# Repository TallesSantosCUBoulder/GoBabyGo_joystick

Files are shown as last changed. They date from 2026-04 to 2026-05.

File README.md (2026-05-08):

# GoBabyGo Joystick-Controlled Car
**ENGR140: First Year Engineering Projects - Colorado Mesa University**  
**Sponsor:** Talles Santos  
**Project Team:** Team Snow Munchers  
**Team Members:** Michael Riley (Civil Engineering)  
&emsp;&emsp;&emsp;&emsp;&emsp;&emsp;&emsp;&emsp; Francisco Cuen (Mechanical Engineering)  
&emsp;&emsp;&emsp;&emsp;&emsp;&emsp;&emsp;&emsp; Jaclyn Pellegrini (Mechanical Engineering)  
&emsp;&emsp;&emsp;&emsp;&emsp;&emsp;&emsp;&emsp;Caleb Kasayka (Mechanical Engineering)  
&emsp;  
&emsp;
&emsp;  
**Note: A large part of this README file references the [User Manual](/Reports/Users%20manual.pdf) and [Final Report](/Reports/Final%20Report%20First%20Draft%20-%20Snow%20Munchers.pdf) written by the members of the Snow Munchers Team. The printed circuit board (PCB) was designed, and the README was written and compiled, by Electrical and Computer Engineering Senior [Alyssa Jackson](https://github.com/aJax-EXE).**

## Introduction
“GoBabyGo” is a non-profit organization dedicated to providing children with limited mobility the opportunity to play independently by adapting motorized toy cars. Many children with mobility challenges struggle to press the pedal and steer simultaneously, making it difficult to operate the vehicle without constant assistance. Typical “GoBabyGo” modifications reroute the pedal wiring to a button mounted on the steering wheel, simplifying acceleration and improving usability.  

After multiple iterations, the final design operated successfully and remained within budget. It reliably controlled forward/backward motion and steering, and testing showed consistent performance with minimal drift. The system was safe, intuitive, and easy for children to use. Future work should focus on simplifying the steering circuit and adapting the design for broader use across different ride‑on car models to benefit more children.  

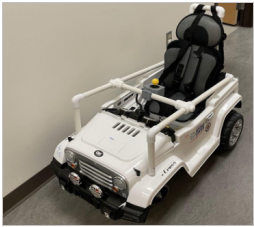
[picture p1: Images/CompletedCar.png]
Image of the Completed Car
  
*A standin image of the completed modified car*  

## Project Overview
While the standard modifications help many children, some still find it difficult to press a button and steer at the same time. This project aims to create a more intuitive control system by replacing both the pedal and steering wheel with a single joystick. The joystick must control forward and backward motion as well as left and right steering, operate safely under 12 V and 3 A, and be implemented for under $200.  

### Design Requirements
Along with the functions that the car needs to reach from the the project overview, the following and specific requirements were needed:  
* Directional Control
    * Provide forward, reverse, left, and right motion; each direction successfully actuates correct motor behavior 10/10 trials with a response rate of .5 seconds. 
* Consistent Steering & Speed Response
    * Vehicle follows the same path in 5 repeated trials within acceptable tolerance (e.g., ±6 inches lateral drift over 10-15ft).
* 12V Maximum Power
    * Must not exceed 12V thought out the electrical system.
* Dashboard Fit
    * Total joystick assembly dimensions must not exceed 2.75 in (height) × 3.125 in (width). Zero interference points and no natural obstructions.
* Heat Limit
    * Must not exceed 113° over 15 minute time intervals.

###  Electrical Solutions
For this car, a modification was made for the movement. Using a joystick instead of a steering wheel and foot-powered pedals, the car can move forwards and backwards without restrictions, but turning left and right is altered. Instead of turning left and right without restriction, moving or holding the joystick in either direction causes the car to turn for only a set amount of time before stopping and waiting for another input. __This is to help keep the motors from stalling as ... ? (Include a video/gif of the car moving in all four directions with the joystick)__  

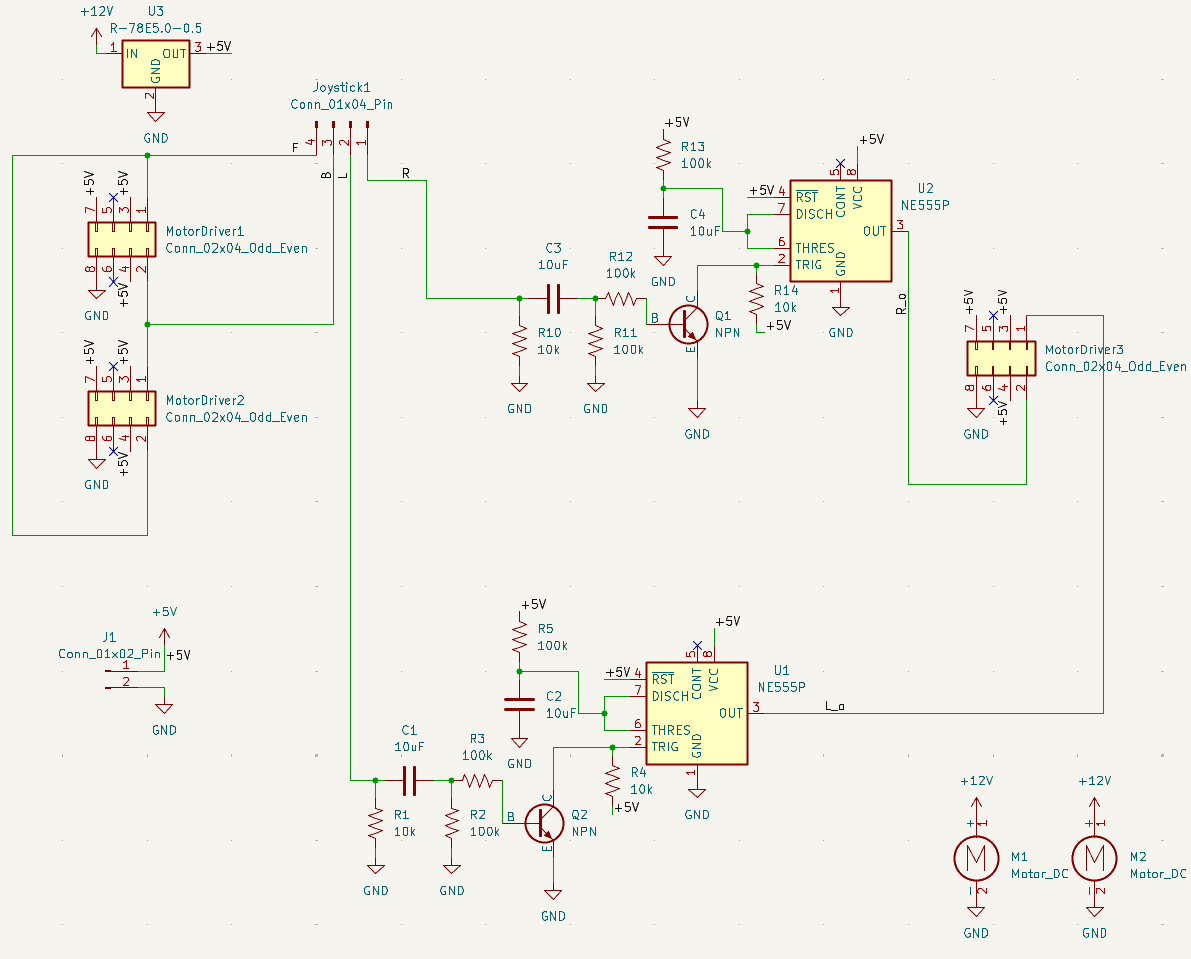
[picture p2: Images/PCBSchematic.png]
Full Car Circuit Diagram
  
*The Full Circuit Diagram of the car*  
&emsp;  

The full construction of the circuit requires the following components:
* [3 IBT-2 BTS7960 High Current H-Bridge Motor Drivers](/Datasheets/BTS7960%20Motor%20Driver.pdf)  
&emsp;  
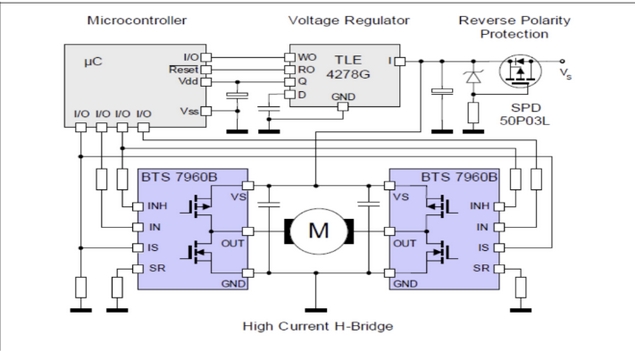
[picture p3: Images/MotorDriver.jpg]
H-Bridge Controller Diagram
      
    *The Function diagram of an H-Bridge Controller*  
    &emsp;  

    * Full representation of the function of an H-Bridge Controller can be found in the above image. When an input is received, it sends a signal to the H-bridge motor controller which recognizes the voltage as a directional input and then outputs that signal into the motor itself. This allows for safe, effective, bi-directional movement. The H-bridge has a total of 12 attachment points. two for power in, two for power to motor, two for input detection (seen as “IN”), two for inhibiting direction (“INH”, two for ISs), a ground for the logic board (GND), and a 5.5V input for the logic board (“VCC”). This design will take advantage of all the inputs / outputs except for the SIs.
* [2 LM555 Timer Chips](/Datasheets/lm555.pdf)  
&emsp;  
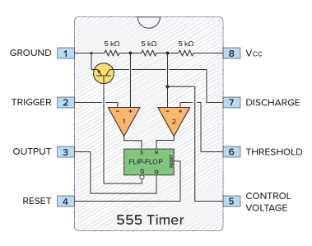
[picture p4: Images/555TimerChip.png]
555 Timer Chip Diagram
      
    *Diagram of a 555 timer and the respective pins*  
    &emsp;  

    * A 555 timer is an integrated circuit that takes an electrical input and outputs a pulse over a certain interval of time. This component is needed to turn the front steering motor to a certain point so that the motor doesn’t overturn the mechanical component, breaking the car, and burning out the motor. Power is inputted through the VCC pin which powers the circuit (as seen in the above image). When a signal comes through the Trigger pin, it goes through the circuit within the 555 and then a capacitor and resistor attached to the discharge and threshold pins which controls how long a pulse is sent out of the output pin. For this project, the 555 is operated in monostable mode, meaning it sends out a singular pulse and then returns to its original state. To get the pulse to last for a certain time, the equation T=1.1RC where T is time, R is the strength of the resistor, and C is the value of the capacitor. For the motor a 1 second pulse is needed so values of a100kΩ resistor and a 10µF capacitor are needed.
* [A Joystick](/Datasheets/SANWA%20JLF-TP-8YT%20Joystick%20Instruction%20Manual.pdf)  
&emsp;  
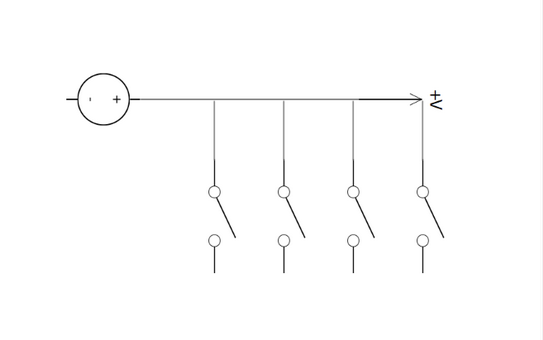
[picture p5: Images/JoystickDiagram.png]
Joystick Switch Diagram
      
    *Internal switching logic of the arcade joystick*  
    &emsp;  

    * The above image illustrates the internal switching logic of the joystick. The joystick has five wires with a gauge of 23 AWG (American Wire Gauge). These wires are connected to a circuit board via a connector. This system consists of four signal wires, each for a different switch that is also connected to the circuit board. The last wire serves as a 5V-12V source wire; the input (5V-12V) will flow through this wire and in return, will output through one of the four switches (possibly two) depending on which switch is compressed or activated. 
* [An RC Car](/Datasheets/BCP%20Sky908%20User%20Manual.pdf)
    * For this project an existing car was bought and provided to the group, but the car model used costs around $250 USD.

* [2 NPN Bipolar Junction Transistors](/Datasheets/2n2222a.pdf)  
&emsp;  
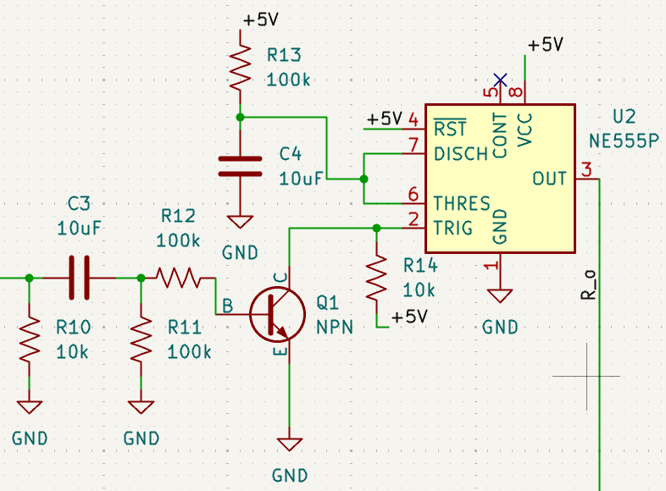
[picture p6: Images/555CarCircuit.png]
Diagram of timing circuit
      
    *The circuit diagram of the pulse shaping module used in the car*  
&emsp;  
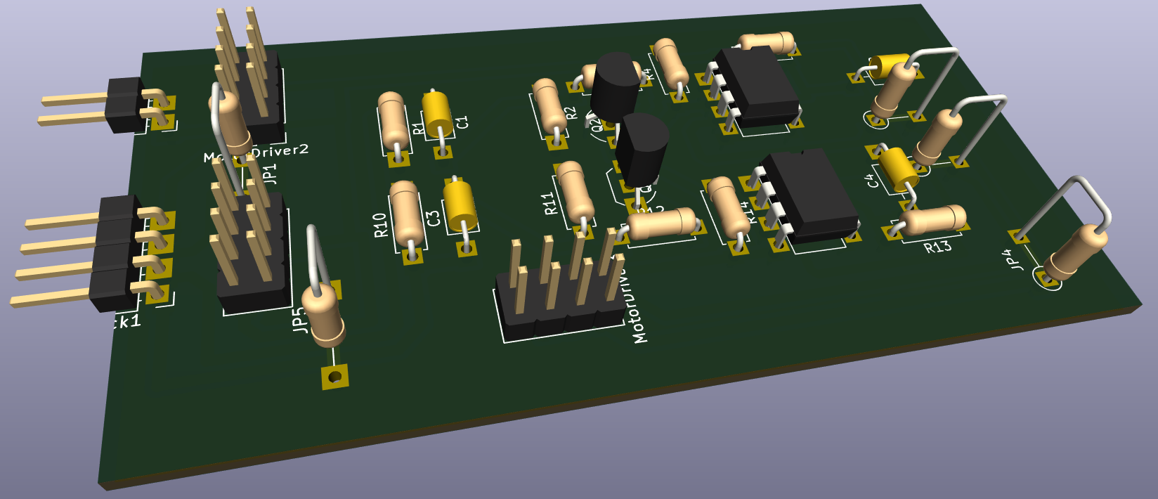
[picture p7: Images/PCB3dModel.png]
3D Model of the working PCB
      
    *The 3D Model that represents what the working model looks like*  
&emsp;  

    * The transistors are the necessary part of the timing circuit. For the 555 to properly work, it needs sharp, high input. This is not as simple as it would seem because our joystick is mainly used in a “toggle” sense, where the driver will hold it left to turn left. After some testing, we realized that this toggled system would lead to the output of the 555 system always being held high. To fix this, we implemented what is called a pulse shaping module. This consists mainly of a capacitor momentarily allowing a transistor to drain a power source to ground, creating a quick pulse of electricity that the 555 timers can properly understand. The above images shows the pulse shaping module implemented into the design of the circuit and the 3D model of the completed PCB with all of its components.  
* [Joystick Mount](/3dModels/Joystick%20Mount%203.STL)
&emsp;  
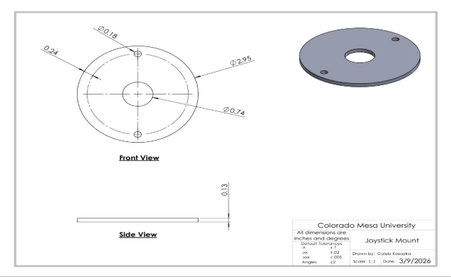
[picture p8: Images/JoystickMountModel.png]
Joystick Mount Solidworks Model
      
    *The SolidWorks drawing of the joystick mount*  
    &emsp;  

    * The joystick already has two existing mounting holes, 0.278 inches in diameter, implemented into the factory design. With this, a CAD drawing was produced and integrated with these existing holes (see Appendix E). The design functions similar to a washer where it will mount on the original steering wheel location. Two bolts will run through the top (the side where the joystick extrudes), and below there will be two nuts securing the simple assembly in place. The above image consists of a SolidWorks drawing of the mount.  
* A 12V to 5V Voltage Step Down
    * Must be able to handle 3A of current and 15W of power.
* 6 100k Ohm Resistors
* 4 10k Ohm Resistors
* 4 10uF Capacitors
* A 12V Battery
    * The model of car used includes a 12V 7AH battery. Most electric kid cars run on 6V, but this system is designed for 12V. To use this system with a 6V battery, a voltage step down that goes from 6V to 5V, or rather a simple voltage divider, needs to be used to run the system properly.
* 2 Rolls of 20 AWG Wire
    * One red and one black preferred.  
* Female to Female Jumper wires  

The circuit starts at the battery going into the two gearboxed motors of the car and the voltage step down. The 5V from the stepdown powers the rest of the system: all three of the motor drivers and the two 555 timer circuits. While the forward and backwards motor drivers are only activated with the direct signal from the joystick, the left and right one first goes through there respective timing circuit to give the proper timed signal.  

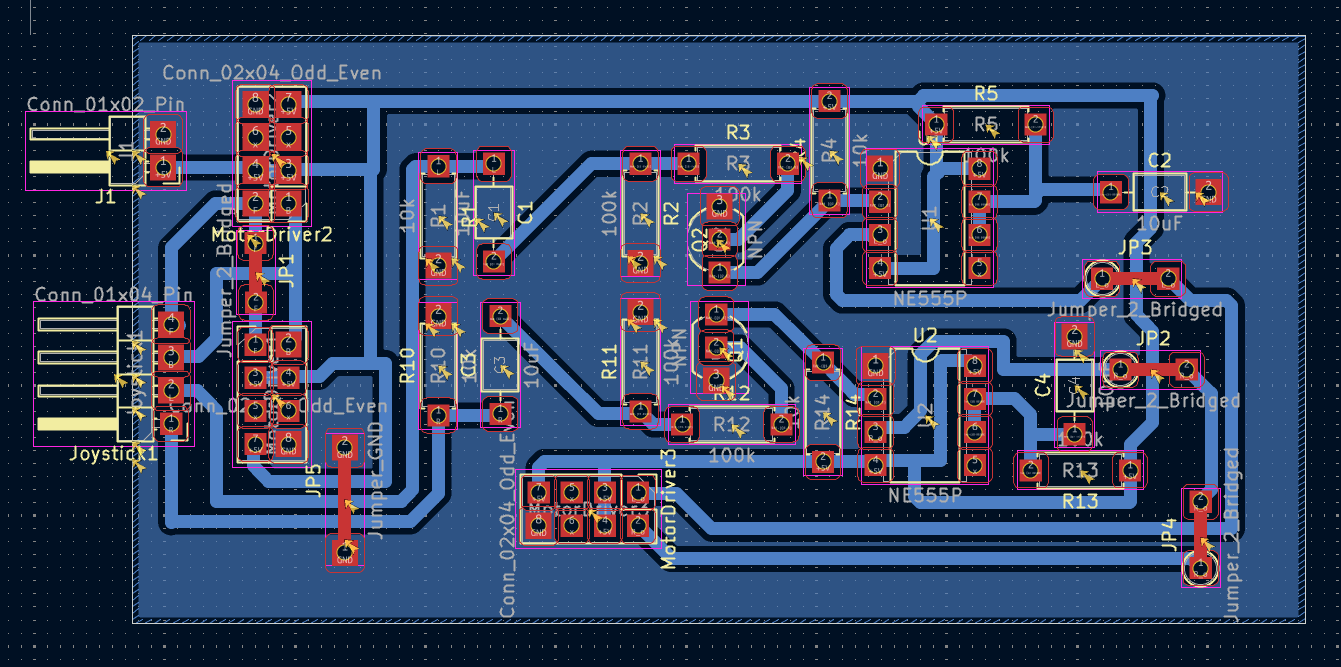
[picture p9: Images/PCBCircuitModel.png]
Full Car PCB Model
  
*The Full PCB model for the car*  
&emsp;  

The PCB holds the resistors, capacitors, and transistors that make up the timing circuit, as well as all of the connectors necessary for both powering the board, connecting the joystick to the motor drivers, and for the motor drivers themselves.

## Hardware Setup and How to Operate
For the complete instructions on how to modify the car to replicate the project, perform maintainence, and for a full list of tools needed and how to use, refer to the [User Manual](/Reports/User%20Manual%20Outline.pdf) written by the Snow Munchers.

### Recommendations for Operation
Before general use, it is recommended that:  
* The driver does not exceed 77lbs
* The car avoids liquid 
* The car is not driven in the rain	 
* The car avoids sharp drops offs like curbs

## Results
### Overview
The electric ride on car was evaluated against the specified design requirements through structed user testing and system performance checks. Each criterion, directional control, steering consistency, power limit, heat limit, and size requirement, was assessed during real world operation to ensure the design met both functional and safety expectations. Users operated the vehicle under normal conditions, allowing the team to observe control, responsiveness, and overall usability. The system was required to satisfy all evaluation criteria in order to be considered successful. Testing results showed that the ride on car met all the design requirements, demonstrating reliable performance, safe operations, and suitability for its intended use.  
&emsp;  
### CRITERIA 1 – DIRECTIONAL CONTROL
Provide forward, reverse, left, and right motion; each direction successfully actuates correct motor behavior 10/10 trials with a response rate of .5 seconds.  

* **PURPOSE OF EVALUATION**: The purpose of the directional control test is to ensure that the electric ride on car responds accurately and reliably to user inputs. Effective directional control is essential for safe operations, as it allows the user to intentionally move the vehicle forward, backward, and laterally, ensuring the car can be maneuvered smoothly during normal operation and while navigating obstacles or turns. 

* **TESTING METHODS**: The evaluation of this design criteria requires that the user manually push the joystick in each direction, forward, backward, left, and right. This was tested in two ways, a static test, elevating the car off a flat surface so that the wheels can spin freely allowing the testers to visually see the steering response. And a dynamic test, driving the car through a specially crafted course designed with turns and corners to test the steering compacity while in motion. For the setup, the car was supported above a flat surface using four wooden 2 by 4 blocks, ensuring that all the wheels were fully suspended and unrestricted in rotation. This configuration eliminated ground friction and external load effects. Allowing isolated evaluation of the motor and steering response. With the vehicle secured, the joystick was actuated individually in the forward, reverse, left, and right directions. Observations were made to confirm correct wheel rotation direction, steering actuation, and immediate system response corresponding to each input. Any unintended motion, delay, or incorrect direction would indicate a fault in the signal interpretation or motor control. For the dynamic control test the electric ride on car was operated on a flat indoor surface and driven through a predefined course designed to replicate realistic operating conditions. The course consisted of straight sections, gradual turns, and sharp corners. Requiring continuous directional input adjustments. The user controlled the vehicle solely via the joystick, executing directional changes while the car remained in motion. This test evaluated the system’s ability to interpret joystick input under load, maintain control during directional transitions, and execute smooth turning without loss of stability or responsiveness. 

* **RESULTS & DISCUSSION**: The electric ride on car demonstrated correct directional response during both static and dynamic testing. In the static response test, joystick inputs in all four directions resulted in correct wheel movement with no observed latency, incorrect rotation, or unintended behavior. During the dynamic testing, the vehicle successfully followed the predetermined course and executed directional changes while in motion. The system maintained full responsiveness and directional accuracy thought out all test runs. No failures or loss of control were observed. As a result, the directional control system achieved a 100% success rate across all tests. The results indicated that the directional control system functions as intended under both unloaded and operational conditions. The static test confirmed control signal interpretation and motor actuation, while the dynamic test verified reliable performance under load. Although quantitative data was not collected, consistent qualitative performance across multiple trials demonstrates that the system meets the directional control requirements. The ability to maintain accurate direction changes while motion indicates sufficient control logic, motor response, and system integration. Therefore, the direction control design requirement was fully satisfied.  

### CRITERIA 2 – STEERING CONSISTENCY
Vehicle follows the same path in 5 repeated trials within acceptable tolerance (e.g., ±6 inches lateral drift over 10-15ft).  

* **PURPOSE OF EVALUATION**: The purpose of the steering consistency requirement is to ensure that the vehicle responds predictably and repeatably and repeatably to identical steering inputs. Consistent steering behavior is essential for user confidence, safe operation, and accurate maneuvering. This requirement verifies that the steering system produces uniform turning behavior without variation or drift during repeated use. 

* **TESTING METHODS**: Steering consistency was assessed using a straight-line deviation test. The vehicle was commanded to drive forward with a fixed joystick input while lateral deviation from a defined centerline was measured. The test evaluates the vehicle’s ability to maintain a straight trajectory under constant input. This method demonstrates whether the steering system produces predictable and repeatable behavior, which directly impacts controllability and user confidence in the finished product. For the setup, the steering consistency test was conducted on a flat, level surface to minimize external influences. A straight reference line was established using a tape measure at a fixed distance placed longitudinally along the test path. The electric ride on was aligned so that its centerline coincided with the reference line at the starting position. The vehicle was positioned at a consistent starting distance for each trial to ensure repeatability. During testing, the car was allowed to travel forward along the reference line while lateral deviation from the centerline was visually monitored and measured relative to the ruler. All tests were performed under identical surface and environment conditions to ensure consistent results. 

* **RESULTS & DISCUSSION**: The straight-line steering consistency test produced lateral drift across multiple trials and test length ranging from approximately 10 – 15ft. measured drift values varied significantly between trials, indicating nonuniform steering behavior under constant joystick input. Server trials remained within the ±6 in acceptance tolerance, deviations were small and showed no progressive drift over the test distance. However few outliers appeared in the tests but they were ruled out for being user error and were taken note of but not deemed important to the over all trials. Within this acceptance range, deviations were small and showed no progressive drift over the test distance. The compliant data demonstrates repeatable straight line tracking performance under consistent input conditions. The in tolerance results indicate that the steering system is capable of maintaining an acceptably straight trajectory when commanded with fixed forward input. The limited magnitude of lateral deviation suggests that the mechanical steering alignment and control response are sufficient for stable, predictable operation in the finished design. These results support the conclusion that, within defined performance limits, the steering system meets the consistency requirement. Maintaining deviation with ±6 inches ensures adequate controllability and user confidence during straight line motion.  

### CRITERIA 3 – POWER LIMIT
Must not exceed 12V thought out the electrical system.  

* **PURPOSE OF EVALUATION**: The purpose of the power limit requirement is to ensure that the electric ride on car operates within safe electric and mechanical limits. Restricted power output prevents excessive speed, reduces stress on system components such as the motor, battery, and drivetrain, and minimizes potential safety risks to the user. This requirement ensures controlled performance while maintaining reliability and compliance with design constraints for the finished project. 

* **TESTING METHODS**: To test, the power limit requirement was evaluated by measuring electrical current and voltage at key point throughout the vehicles electrical system. A multimeter was used to monitor voltage and current in selected wiring segments supplying the motor and control electronics during operation. Testing verified that system voltage remained below 12 V and that operating current did not exceed the specified limit of a 3 amp under normal driving conditions. Measurements were taken while the vehicle was powered and active to ensure compliance under realistic load conditions. For the setup, power limit testing was conducted using a digital multimeter to measure voltage and current at multiple points within the vehicle’s electrical system. Measurement locations included the batter output, motor supply lines, and control circuit wiring to capture representative operating conditions. The car was powered on and operated under normal operating conditions while the multimeter probes were connected in series for current measurement and in parallel for voltage measurement. Tests were performed while the vehicle was stationary and during motion to account for load variation. All measurements were taken with the system fully assembled to reflect real operating conditions. 

* **RESULTS & DISCUSSION**: Power limit testing confirmed that the electrical system operated within the defined constraints during all the testing conditions. Measured system voltage remained below the maximum allowable limit of 12V, and operating current did not exceed 3 amps at any monitored location. All measurements points across the battery, motor supply, and control wiring remained within the specified limits under both stationary and dynamic operating conditions, as a results, the power limit requirements was successfully met for all tests. The results confirm that the electrical power system operates within the specified voltage and current limits under normal operating conditions. Maintaining voltage below 12 V and current at or below 3 amps ensures safe operation of the motor and control electronics while reducing the risk of overheating, electrical stress, and components failure. Compliance with the power limit requirement indicates that the selected electrical components and system configuration are appropriately matched to the vehicle’s performance needs. This controlled power outage contributes to overall system reliability and user safety, supporting the suitability of the design for its intended application.  

### CRITERIA 4 – HEAT LIMIT
Must not exceed 113° over 15 minute time intervals.  

* **PURPOSE OF EVALUATION**: The purpose of the heat limit requirement is to ensure that the electrical and mechanical components of the electric ride on car operate within safe temperature ranges during normal use. Limiting heat buildup prevents thermal damage, reduced the risk of components failure, ensures user safety. This requirements supports system reliability longevity and consistent performance throughout operation. 

* **TESTING METHODS**: The heat limit requirement was evaluated by monitoring temperature during sustained operation. An Arduino based temperature sensing system was connected to the motor to continuously monitor thermal performance. The motor was operated continuously for a duration of 15 minutes under normal operating conditions. Temperature readings were observed to determine whether the motor temperature remained below the maximum allowable limit of 113 °F throughout the test period. For the setup, the heat limit was conducted using an Arduino microcontroller interfaced with a temperature sensor mounted directly to the motor casing to measure operating temperature. The sensor was secured to ensure consistent thermal contact and accurate temperature readings throughout the test. The electric ride on car was placed in a stationary configuration to allow continuous motor operation without external interruptions. Power was supplied under normal operating voltage, and the motors were run continuously for a 15 minute duration. Temperature reading were monitored in real time through the Arduino system to verify that the motor temperature remained below the maximum allowable limit of 113 °F for the entire test period.

* **RESULTS & DISCUSSION**: The heat limit requirement was considered satisfied based on qualitative observation during vehicle operation. Although a full 15 minute controlled temperature test was not completed due to time constraints, the motor was operated during multiple system tests without exhibiting signs of excessive heat build up. Though these test, the motor maintained stable performance with no observable thermal degradation, shut down, or adverse response related to heat generation. Based on the motors behavior during externed use and the absence of overheating indicators, the system was determined to operate within acceptable thermal limits. Although a full duration heat test was not completed, the observed system behavior during extended operations indicted that the motor operates within acceptable thermal limits. The absence of thermal issues during sustained use suggests that the selected motor and power configuration are sufficient for the intended operating conditions. While additional quantitative temperature data would strengthen validation, the qualitative results support the conclusion that the heat generation does not pose a safety or reliability concern for the current design. Future testing with continuous temperature logging over longer duration recommended to further validate thermal performance and confirm compliance under all operating scenarios.  

### CRITERIA 5 – SIZE REQUIREMENT
Total joystick assembly dimensions must not exceed 2.75 in (height) × 3.125 in (width). Zero interference points and no natural obstructions.  

* **PURPOSE OF EVALUATION**: The joystick components were required to fit within a designated envelope of 2.75in x 3.125 in space to ensure proper integration with the vehicle. Maintaining this size constraints prevents interference with vehicle operation, preserved drivability, and reduced the likelihood of accidental contact or mechanical damage during regular use. A compact fit also supports ergonomic accessibility for the user while allowing the control system to be securely mounted and protected within the vehicle structure.  

* **TESTING METHODS**: Size evaluation was conducted through a physical fitment verification and user interaction testing. The control circuit board was designed and assembled to conform to the allocated  dashboard of  2.75 in x 3.125 in. prior to permeant installation, the joystick components were temporally secured in the location using tape to allow visual and dimensional comparison with he available space. Once loosely secured, the vehicle was operated in a simulated use scenario. Testers interacted with the ride on car as a child user would, ensuring that the joystick and associated components did not obstruct operation, restrict movement, or practical useability of the installed parts.

* **RESULTS & DISCUSSION**: During size evaluation, the joystick mount component required four design iterations due to improper fit within the allocated dashboard space. Each reprint addressed dimensional and alignment issues until the final mount achieved a secure and accurate fit. The circuit board and associated wiring were successfully integrated within the design rea and remained neatly secured throughout testing. No components were exposed or positioned in a way that could be easily accessed or damaged during normal use. Once fully installed, all components fit securely within the available space without requiring further adjustment. These results confirm that the size requirement was met in the final configuration. Safe security of critical control components ensures the physical compatibly with the vehicle and is suitable for real-world use. Proper fitment directly affects drivability, user interaction, and long-term durability. Particularly in a ride on device intended for child use. Components that excess the allocated space or are improperly positioned introduce risks of accidental contact, interference during operation, or mechanical damage over time. The testing approach verifies dimensional compliance, simulating realistic user interaction. Supporting safe operation and reinforcing the overall robustness of the design.  

### Conclusion 
The electric ride on car joystick integration designed by the Snow Munchers team wad successfully evaluated against the defined design requirement using a combination of user testing, qualitative observation, and targeted system checks. The vehicle demonstrated reliable directional control and acceptable steering consistency under controlled testing conditions. Supporting predictable and safe maneuverability. Electric testing confirmed operation within the specified power limits, ensuring system safety and component reliability. Thermal performance did not present observable issues during extended operation, indicating the heat generation remains within acceptable bounds for the intended use. Additionally, the control components were successfully integrated within the allocated size constraints, preventing interference with drivability and reducing the risk of damage during regular use. Indicating the final design meets the primary functional, safety, and usability criteria created for the projects solid foundation and future refinement.  
&emsp;  

## Next Steps
Firstly, the telecontrol should be reattached. This feature was initially implemented into the car for safety, but the snow munchers did not have time to fully integrate this. To re-implement this feature, a second PCB would have to be printed to allow for toggleable control between the IBT-2 motor drivers and the standard relay. This could be done most simplistically with 4 transistors for each motor. Two to allow for flow from the telecontrol relay and the other two to allow for flow from the joystick. The second reintegration should be rewiring the lights. The old lights are already attached and ready to run, however they need to be wired to a new power to turn on with the car. Similarly, the sound system can be easily repaired; however, the old speaker was damaged when removed, so a replacement would need to be purchased and reinstalled inside the dashboard.

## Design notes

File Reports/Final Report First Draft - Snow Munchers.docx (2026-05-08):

Adapting The Throttle & Steering Controls of a Motorized Toy Car to a Joystick Interface

Francisco Cuen, Michael Riley, Jaclyn Pellegrini, Caleb Kasayka

The Snow Munchers & GoBabyGo

Colorado Mesa University

Table of Contents

3. Executive Summary.....................................................................................1
4. Problem Definition....................................................................................2-3
  4.1. PROBLEM SCOPE
  4.2. TECHNICAL REVIEW
    4.2.1. BACKGROUND
    4.2.2. EXISTING SOLUTIONS
  4.3. DESIGN REQUIREMENTS & CRITERIA
5. Design Description....................................................................................3-6
  5.1. OVERVIEW
  5.2. DETAILED DESCRIPTION
    5.2.1. JOYSTICK
    5.2.2. JOYSTICK MOUNT
    5.2.3. PRINTED CIRCUIT BOARD (PCB)
    5.2.4. H-BRIDGE CONTROLLER
    5.2.5. 555 TIMER
    5.2.6. PULSE SHAPING MODULE
6. Design Evaluation...................................................................................6-12
  6.1. OVERVIEW
    6.1.1. CRITERIA 1 – DIRECTIONAL CONTROL
      6.1.1.1. PURPOSE OF EVALUATION
      6.1.1.2. TESTING METHODS
      6.1.1.3. RESULTS & DISCUSSIONS
    6.1.2. CRITERIA 2 – STEERING CONSISTENCY
    6.1.3. CRITERIA 3 – POWER LIMIT
    6.1.4. CRITERIA 4 – HEAT LIMIT
    6.1.5. CRITERIA 5 – SIZE REQUIREMENT
7. Team Performance.....................................................................................13
8. Conclusions & Recommendations............................................................13
  8.1. RECOMMENDATIONS
  8.2. RECOMMENDED NEXT STEPS
9. References...................................................................................................14
10. Appendices............................................................................................15-18
3. Executive Summary

Background

“GoBabyGo” is a non-profit organization dedicated to providing children with limited mobility the opportunity to play independently by adapting motorized toy cars. Many children with mobility challenges struggle to press the pedal and steer simultaneously, making it difficult to operate the vehicle without constant assistance. Typical “GoBabyGo” modifications reroute the pedal wiring to a button mounted on the steering wheel, simplifying acceleration and improving usability.

Project Purpose

While the standard modifications help many children, some still find it difficult to press a button and steer at the same time. This project aims to create a more intuitive control system by replacing both the pedal and steering wheel with a single joystick. The joystick must control forward and backward motion as well as left and right steering, operate safely under 12 V and 3 A, and be implemented for under $200.

Design Selected

Because the team had limited electrical engineering experience, simplicity was a major design priority. The final design used a circuit that routed power through the joystick. When the forward or backward button was pressed, the joystick sent power to an H-bridge motor controller, which drove the rear motor in the appropriate direction. Steering was controlled by a second H-bridge connected to the front motor. To prevent mechanical damage from over-rotation, the joystick sent timed pulses rather than continuous power. This was achieved using 555 timers and a pulse shaping module that generated the negative pulse required for proper 555 operation.

Results & Conclusions

After multiple iterations, the final design operated successfully and remained within budget. It reliably controlled forward/backward motion and steering, and testing showed consistent performance with minimal drift. The system was safe, intuitive, and easy for children to use. Future work should focus on simplifying the steering circuit and adapting the design for broader use across different ride-on car models to benefit more children.

4. Problem Definition
  4.1. PROBLEM SCOPE

This paper documents the redesign of a motorized toy car by adapting the controls to run via a joystick for the program “GoBabyGo!”. They are an organization at Colorado Mesa University that aims to aid in the issue of children—with limited mobility—not being able to utilize normal motorized kid cars. This idea of adapting a joystick controller is founded on the original “GoBabyGo!” adaptation of replacing the traditional “gas” pedal with a switch-powered button located on the steering wheel [1]. The issue with this different access for independent mobility is that there are children with limited mobility in the sense that they cannot maneuver the traditional steering wheel while simultaneously pressing the button to move the car. With this realization, Dr. Santos, the head of “GoBabyGo!” tasked the Snow Munchers, with the development of this joystick controller to access the “go” motion and steering all in one component. This makes the operation of the car more intuitive and user friendly for the client.

  4.2. TECHNICAL REVIEW
    4.2.1. BACKGROUND: “GoBabyGo!” is a charitable program that takes ride-on toy cars and modifies them for children with limited mobility problems. Their intent is to promote independence, exploration, and play in children who might struggle in these areas due to their limited mobility. In the past, many electric kids' cars have been modified for children with limited mobility, most commonly by removing the gas pedal and attaching a button to the steering wheel that controls the “go.” (As seen in Appendix A) [2]. This is a great modification for children with limited mobility in their lower limbs, but this does not consider the children with limited mobility in their hands and arms and is not very intuitive. The steering wheel is still a problem for them as they cannot push the button and steer the wheel at the same time, which keeps them from operating these cars at the independent level which they want to.
    4.2.2. EXISTING SOLUTIONS: By no means are the Snow Munchers the first ones to create a children's car controlled by a joystick. There have been several other designs made over the years where engineers have implemented a joystick to control the movements of cars that are very similar to the Snow Munchers. An example of this is Autodesk’s “Make a Joystick-controlled Ride-on Car” (as seen in Appendix B) which controls the steering and go through a microcontroller and other complicated electronics. [3] The issue with designs like these is that they are costly and more complicated as a microcontroller needs coding and complicates the system. The Snow Munchers design avoids replacing the control unit in the car by removing the old input methods, steering wheel and gas pedal, and diverting the wires to the joystick then through a circuit which connects to H-bridge motor controllers to control the forward, backward, and steering motors. This allows us to cut out buying a new control unit or coding a microcontroller. This cuts down on complexity and cost immensely. This is reflected by the fact that past designs like the “Autodesk” model cost upwards of $300.
  4.3. DESIGN REQUIREMENTS & CRITERIA

The project deliverable is an optimized joystick controlled system that replaces the original steering wheel and pedal interface of a child’s electric ride-on car. The system must meet the following measurable design requirements:

- Directional Control
  - Requirement: Provide forward, reverse, left, and right motion; each direction successfully actuates correct motor behavior 10/10 trials with a response rate of .5 second.
- Consistent Steering & Speed Response
  - Requirement: Vehicle follows the same path in 5 repeated trials within acceptable tolerance (e.g., ±6 inches lateral drift over 10-15ft).
- 10. 12V Maximum Power
  - Requirement: Must not exceed 12V thought out the electrical system.
- Dashboard Fit
  - Requirement: Total joystick assembly dimensions must not exceed 2.75 in (height) × 3.125 in (width). Zero interference points and no natural obstructions.
- Heat Limit
  - Requirement: Must not exceed 113° over 15 minute time intervals.
5. Design Description
  5.1. OVERVIEW

The joy-stick integrated kid car is a redesign of traditional steering and throttle controls. The functioning portion of this new joystick is implemented into the car’s original wiring circuit using a H-Bridge DC Motor Controller. For each positive or negative x and y direction, the joystick assigns all four switches to one specific direction. With each input, this will signal power for the throttle through the H-Bridge motor controller and also steering motor controls. For use on the car, it is simply mounted on the dashboard using nuts and bolts, and the corresponding 3D printed mount (eventually machined out of carbon steel). Appendix C represents a block diagram of the circuit.

  5.2. DETAILED DESCRIPTION
    5.2.1. JOYSTICK - The joystick has five wires with a gauge of 23 AWG (American Wire Gauge). These wires are connected to a circuit board via a connector. This system consists of four signal wires, each for a different switch that is also connected to the circuit board. The last wire (supply wire as seen in Appendix D) serves as a 5v-12v source wire; the input (5v-12v) will flow through this wire and in return, will output through one of the four switches (possibly two) depending on which switch is compressed or activated. Appendix D illustrates the internal switching logic of the joystick.
    5.2.2. JOYSTICK MOUNT - The joystick already has two existing mounting holes, 0.278 inches in diameter, implemented into the factory design. With this, a CAD drawing was produced and integrated with these existing holes (see Appendix E). The design functions similar to a washer where it will mount on the original steering wheel location. Two bolts will run through the top (the side where the joystick extrudes), and below there will be two nuts securing the simple assembly in place. Appendix E consists of a SolidWorks drawing of the mount.
    5.2.3. PRINTED CIRCUIT BOARD (PCB) - The circuit board serves as the central control interface between the joystick input and the motorized drive system of the adapted ride on car. This subsystem houses the H-bridge motor controller and 555 Timer. It provides organized electrical connections between the joystick, power supply, and DC motors. Its primary function is to safely and reliably control the direction and motion of the vehicle while meeting accessibility and safety design criteria. Refer to Appendix I to see the board.
    5.2.4. H-BRIDGE CONTROLLER - When an input is received, it sends a signal to the H-bridge motor controller which recognizes the voltage as a directional input and then outputs that signal into the motor itself. This allows for safe, effective, bi-directional movement. The H-bridge has a total of 12 attachment points. two for power in, two for power to motor, two for input detection (seen as “IN” in Appendix F), two for inhibiting direction (“INH” in Appendix F, two for ISs (seen in Appendix F), a ground for the logic board (GND in Appendix F), and a 5.5V input for the logic board (“VCC” in Appendix F). This design will take advantage of all the inputs / outputs except for the SIs. Full representation of the function of an H-Bridge Controller can be found in Appendix F.
    5.2.5. 555 TIMER - A 555 timer is an integrated circuit that takes an electrical input and outputs a pulse over a certain interval of time. [4] This component is needed to turn the front steering motor to a certain point so that the motor doesn’t overturn the mechanical component, breaking the car, and burning out the motor. Power is inputted through the VCC pin which powers the circuit (as seen in Appendix G). When a signal comes through the Trigger pin, it goes through the circuit within the 555 and then a capacitor and resistor attached to the discharge and threshold pins which controls how long a pulse is sent out of the output pin. For this project, the 555 is operated in monostable mode, meaning it sends out a singular pulse and then returns to its original state. To get the pulse to last for a certain time, the equation T=1.1RC where T is time, R is the strength of the resistor, and C is the value of the capacitor. For the motor a 1 second pulse is needed so values of a100kΩ resistor and a 10µF capacitor are needed. [5]
    5.2.6. PULSE SHAPING MODULE - For the 555 to properly work, it needs sharp, high input. This is not as simple as it would seem because our joystick is mainly used in a “toggle” sense, where the driver will hold it left to turn left. After some testing, we realized that this toggled system would lead to the output of the 555 system always being held high. To fix this, we implemented what is called a pulse shaping module. This consists mainly of a capacitor momentarily allowing a transistor to drain a power source to ground, creating a quick pulse of electricity that the 555 timers can properly understand. Appendix H shows the pulse shaping module implemented into the design of the circuit. Appendix I contains a picture of all components from 5.2.5 to 5.2.6 on the working PCB.
  5.3. USE

This design is intended to serve as an alternative to the standard electric toy car currently available on the market for children. Vehicle control is achieved through a joystick interface that replaces both steering and throttle functions. When the user pushes up, down, right, or left on the joystick, the car will accelerate or turn towards the given direction. This method allows the user to interact with the vehicle in a more intuitive and accessible manner. Additionally, this design also aids in the issue that some children may have, where they cannot operate the standard toy car controls independently.

See Appendix J for Bill of Materials for the cost estimate of these components

(excluding the price of the car).

6. Design Evaluation
  6.1. OVERVIEW

The electric ride on car was evaluated against the specified design requirements through structed user testing and system performance checks. Each criterion, directional control, steering consistency, power limit, heat limit, and size requirement, was assessed during real world operation to ensure the design met both functional and safety expectations. Users operated the vehicle under normal conditions, allowing the team to observe control, responsiveness, and overall usability. The system was required to satisfy all evaluation criteria in order to be considered successful. Testing results showed that the ride on car met all the design requirements, demonstrating reliable performance, safe operations, and suitability for its intended use.

  6.2. CRITERIA 1 – DIRECTIONAL CONTROL

Table 1. Testing requirements, outcomes, and testing methods for the requirements for directional control. Requirement – must have fully functional control over the direction of the moving car.

    6.2.1. PURPOSE OF EVALUATION - The purpose of the directional control test is to ensure that the electric ride on car responds accurately and reliably to user inputs. Effective directional control is essential for safe operations, as it allows the user to intentionally move the vehicle forward, backward, and laterally, ensuring the car can be maneuvered smoothly during normal operation and while navigating obstacles or turns.
    6.2.2. TESTING METHODS - The evaluation of this design criteria requires that the user manually push the joystick in each direction, forward, backward, left, and right. This was tested in two ways, a static test, elevating the car off a flat surface so that the wheels can spin freely allowing the testers to visually see the steering response. And a dynamic test, driving the car through a specially crafted course designed with turns and corners to test the steering compacity while in motion. For the setup, the car was supported above a flat surface using four wooden 2 by 4 blocks, ensuring that all the wheels were fully suspended and unrestricted in rotation. This configuration eliminated ground friction and external load effects. Allowing isolated evaluation of the motor and steering response. With the vehicle secured, the joystick was actuated individually in the forward, reverse, left, and right directions. Observations were made to confirm correct wheel rotation direction, steering actuation, and immediate system response corresponding to each input. Any unintended motion, delay, or incorrect direction would indicate a fault in the signal interpretation or motor control. For the dynamic control test the electric ride on car was operated on a flat indoor surface and driven through a predefined course designed to replicate realistic operating conditions. The course consisted of straight sections, gradual turns, and sharp corners. Requiring continuous directional input adjustments. The user controlled the vehicle solely via the joystick, executing directional changes while the car remained in motion. This test evaluated the system’s ability to interpret joystick input under load, maintain control during directional transitions, and execute smooth turning without loss of stability or responsiveness.
    6.2.3. RESULTS & DISCUSSION - The electric ride on car demonstrated correct directional response during both static and dynamic testing. In the static response test, joystick inputs in all four directions resulted in correct wheel movement with no observed latency, incorrect rotation, or unintended behavior. During the dynamic testing, the vehicle successfully followed the predetermined course and executed directional changes while in motion. The system maintained full responsiveness and directional accuracy thought out all test runs. No failures or loss of control were observed. As a result, the directional control system achieved a 100% success rate across all tests. The results indicated that the directional control system functions as intended under both unloaded and operational conditions. The static test confirmed control signal interpretation and motor actuation, while the dynamic test verified reliable performance under load. Although quantitative data was not collected, consistent qualitative performance across multiple trials demonstrates that the system meets the directional control requirements. The ability to maintain accurate direction changes while motion indicates sufficient control logic, motor response, and system integration. Therefore, the direction control design requirement was fully satisfied.
  6.3. CRITERIA 2 – STEERING CONSISTENCY
    6.3.1. PURPOSE OF EVALUATION - The purpose of the steering consistency requirement is to ensure that the vehicle responds predictably and repeatably and repeatably to identical steering inputs. Consistent steering behavior is essential for user confidence, safe operation, and accurate maneuvering. This requirement verifies that the steering system produces uniform turning behavior without variation or drift during repeated use.
    6.3.2. TESTING METHODS - Steering consistency was assessed using a straight-line deviation test. The vehicle was commanded to drive forward with a fixed joystick input while lateral deviation from a defined centerline was measured. The test evaluates the vehicle’s ability to maintain a straight trajectory under constant input. This method demonstrates whether the steering system produces predictable and repeatable behavior, which directly impacts controllability and user confidence in the finished product. For the setup, the steering consistency test was conducted on a flat, level surface to minimize external influences. A straight reference line was established using a tape measure at a fixed distance placed longitudinally along the test path. The electric ride on was aligned so that its centerline coincided with the reference line at the starting position. The vehicle was positioned at a consistent starting distance for each trial to ensure repeatability. During testing, the car was allowed to travel forward along the reference line while lateral deviation from the centerline was visually monitored and measured relative to the ruler. All tests were performed under identical surface and environment conditions to ensure consistent results.
    6.3.3. RESULTS & DISCUSSION - The straight-line steering consistency test produced lateral drift across multiple trials and test length ranging from approximately 10 – 15ft. measured drift values varied significantly between trials, indicating nonuniform steering behavior under constant joystick input. Server trials remained within the ±6 in acceptance tolerance, deviations were small and showed no progressive drift over the test distance. However few outliers appeared in the tests but they were ruled out for being user error and were taken note of but not deemed important to the over all trials. Within this acceptance range, deviations were small and showed no progressive drift over the test distance. The compliant data demonstrates repeatable straight line tracking performance under consistent input conditions. The in tolerance results indicate that the steering system is capable of maintaining an acceptably straight trajectory when commanded with fixed forward input. The limited magnitude of lateral deviation suggests that the mechanical steering alignment and control response are sufficient for stable, predictable operation in the finished design. These results support the conclusion that, within defined performance limits, the steering system meets the consistency requirement. Maintaining deviation with ±6 inches ensures adequate controllability and user confidence during straight line motion.
  6.4. CRITERIA 3 – POWER LIMIT
    6.4.1. PURPOSE OF EVALUATION - The purpose of the power limit requirement is to ensure that the electric ride on car operates within safe electric and mechanical limits. Restricted power output prevents excessive speed, reduces stress on system components such as the motor, battery, and drivetrain, and minimizes potential safety risks to the user. This requirement ensures controlled performance while maintaining reliability and compliance with design constraints for the finished project.
    6.4.2. TESTING METHODS - To test, the power limit requirement was evaluated by measuring electrical current and voltage at key point throughout the vehicles electrical system. A multimeter was used to monitor voltage and current in selected wiring segments supplying the motor and control electronics during operation. Testing verified that system voltage remained below 12 V and that operating current did not exceed the specified limit of a 3 amp under normal driving conditions. Measurements were taken while the vehicle was powered and active to ensure compliance under realistic load conditions. For the setup, power limit testing was conducted using a digital multimeter to measure voltage and current at multiple points within the vehicle’s electrical system. Measurement locations included the batter output, motor supply lines, and control circuit wiring to capture representative operating conditions. The car was powered on and operated under normal operating conditions while the multimeter probes were connected in series for current measurement and in parallel for voltage measurement. Tests were performed while the vehicle was stationary and during motion to account for load variation. All measurements were taken with the system fully assembled to reflect real operating conditions.
    6.4.3. RESULTS & DISCUSSION - Power limit testing confirmed that the electrical system operated within the defined constraints during all the testing conditions. Measured system voltage remained below the maximum allowable limit of 12V, and operating current did not exceed 3 amps at any monitored location. All measurements points across the battery, motor supply, and control wiring remained within the specified limits under both stationary and dynamic operating conditions, as a results, the power limit requirements was successfully met for all tests. The results confirm that the electrical power system operates within the specified voltage and current limits under normal operating conditions. Maintaining voltage below 12 V and current at or below 3 amps ensures safe operation of the motor and control electronics while reducing the risk of overheating, electrical stress, and components failure. Compliance with the power limit requirement indicates that the selected electrical components and system configuration are appropriately matched to the vehicle’s performance needs. This controlled power outage contributes to overall system reliability and user safety, supporting the suitability of the design for its intended application.
  6.5. CRITERIA 4 – HEAT LIMIT
    6.5.1. PURPOSE OF EVALUATION - The purpose of the heat limit requirement is to ensure that the electrical and mechanical components of the electric ride on car operate within safe temperature ranges during normal use. Limiting heat buildup prevents thermal damage, reduced the risk of components failure, ensures user safety. This requirements supports system reliability longevity and consistent performance throughout operation.
    6.5.2. TESTING METHODS - The heat limit requirement was evaluated by monitoring temperature during sustained operation. An Arduino based temperature sensing system was connected to the motor to continuously monitor thermal performance. The motor was operated continuously for a duration of 15 minutes under normal operating conditions. Temperature readings were observed to determine whether the motor temperature remained below the maximum allowable limit of 113 °F throughout the test period. For the setup, the heat limit was conducted using an Arduino microcontroller interfaced with a temperature sensor mounted directly to the motor casing to measure operating temperature. The sensor was secured to ensure consistent thermal contact and accurate temperature readings throughout the test. The electric ride on car was placed in a stationary configuration to allow continuous motor operation without external interruptions. Power was supplied under normal operating voltage, and the motors were run continuously for a 15 minute duration. Temperature reading were monitored in real time through the Arduino system to verify that the motor temperature remained below the maximum allowable limit of 113 °F for the entire test period.
    6.5.3. RESULTS & DISCUSSION - The heat limit requirement was considered satisfied based on qualitative observation during vehicle operation. Although a full 15 minute controlled temperature test was not completed due to time constraints, the motor was operated during multiple system tests without exhibiting signs of excessive heat build up. Though these test, the motor maintained stable performance with no observable thermal degradation, shut down, or adverse response related to heat generation. Based on the motors behavior during externed use and the absence of overheating indicators, the system was determined to operate within acceptable thermal limits. Although a full duration heat test was not completed, the observed system behavior during extended operations indicted that the motor operates within acceptable thermal limits. The absence of thermal issues during sustained use suggests that the selected motor and power configuration are sufficient for the intended operating conditions. While additional quantitative temperature data would strengthen validation, the qualitative results support the conclusion that the heat generation does not pose a safety or reliability concern for the current design. Future testing with continuous temperature logging over longer duration recommended to further validate thermal performance and confirm compliance under all operating scenarios.
  6.6. CRITERIA 5 – SIZE REQUIREMENT
    6.6.1. PURPOSE OF EVALUATION - The joystick components were required to fit within a designated envelope of 2.75in x 3.125 in space to ensure proper integration with the vehicle. Maintaining this size constraints prevents interference with vehicle operation, preserved drivability, and reduced the likelihood of accidental contact or mechanical damage during regular use. A compact fit also supports ergonomic accessibility for the user while allowing the control system to be securely mounted and protected within the vehicle structure.
    6.6.2. TESTING METHODS - Size evaluation was conducted through a physical fitment verification and user interaction testing. The control circuit board was designed and assembled to conform to the allocated dashboard of 2.75 in x 3.125 in. prior to permeant installation, the joystick components were temporally secured in the location using tape to allow visual and dimensional comparison with he available space. Once loosely secured, the vehicle was operated in a simulated use scenario. Testers interacted with the ride on car as a child user would, ensuring that the joystick and associated components did not obstruct operation, restrict movement, or practical useability of the installed parts.
    6.6.3. RESULTS & DISCUSSION - During size evaluation, the joystick mount component required four design iterations due to improper fit within the allocated dashboard space. Each reprint addressed dimensional and alignment issues until the final mount achieved a secure and accurate fit. The circuit board and associated wiring were successfully integrated within the design rea and remained neatly secured throughout testing. No components were exposed or positioned in a way that could be easily accessed or damaged during normal use. Once fully installed, all components fit securely within the available space without requiring further adjustment. These results confirm that the size requirement was met in the final configuration. Safe security of critical control components ensures the physical compatibly with the vehicle and is suitable for real-world use. Proper fitment directly affects drivability, user interaction, and long-term durability. Particularly in a ride on device intended for child use. Components that excess the allocated space or are improperly positioned introduce risks of accidental contact, interference during operation, or mechanical damage over time. The testing approach verifies dimensional compliance, simulating realistic user interaction. Supporting safe operation and reinforcing the overall robustness of the design.
    6.6.4. CONCLUSION - The electric ride on car joystick integration designed by the Snow Munchers team wad successfully evaluated against the defined design requirement using a combination of user testing, qualitative observation, and targeted system checks. The vehicle demonstrated reliable directional control and acceptable steering consistency under controlled testing conditions. Supporting predictable and safe maneuverability. Electric testing confirmed operation within the specified power limits, ensuring system safety and component reliability. Thermal performance did not present observable issues during extended operation, indicating the heat generation remains within acceptable bounds for the intended use. Additionally, the control components were successfully integrated within the allocated size constraints, preventing interference with drivability and reducing the risk of damage during regular use. Indicating the final design meets the primary functional, safety, and usability criteria created for the projects solid foundation and future refinement.
7. Team Performance

The initial impression from the Snow Munchers of the complexity of this project was nowhere near the level that is seen in their product. Given this, the change in the amount of project planning, scheduling, and research was directly proportional to the increase in labor it took to complete the adaptation. Each additional component resulted in a delay by having to wait for parts, revise the circuit, and most importantly fitting times in the team's Gantt Chart (see Appendix K). Progression through the project had shifted the team dynamic to a "divide and conquer” approach. The members who could easily access the project consistently helped utilize their time by meeting with outside resources or by physically working on the project. The remaining members were tasked with taking record of progress, maintaining schedule, and researching necessary data. While the workload may not have been split evenly, it was still divided fairly amongst all the members. When in doubt, check the Gantt chart. With deadlines approaching, meeting times extending, and attendance beginning to falter, they needed to pay close attention to the vital deadlines they planned via their Gantt Chart. This tool helped the find common ground when progression was behind schedule, or deadlines were closer than expected. If needed, the volume of workload given to a team member was relieved by the team to stay on schedule and to preserve the quality aspect of that specific assignment. While the Gantt Chart was made at the start of the project when there were less tasks expected, the tool was still not sent to waste. Rather than taking time to fully revise the chart for additional tasks, it was wiser to put that energy into other areas. By simply taking note of the deadlines or planning workarounds for these time constraints, the chart was still utilized as a guideline and would also highlight how the team was performing.

8. Conclusions & Recommendations

Over the course of this project, the Snow Munchers were able to achieve the goal they had set out for: creating a kid's electric ride-on car controlled by only a joystick. This may sound simple, but it required completely rewiring the vehicle, designing and manufacturing a mount for the joystick, troubleshooting a PCB (printed circuit board), and vigorous testing to ensure the safety of the driver. The final product does fall slightly short of what the car used to be, however. Due to the trickiness of this project and tight schedule, the telecontrol had to be removed all together and the lights and speakers were disabled. While this is unfortunate, the project was ultimately successful in completing the goal. On top of this, all the old components are still functioning and have been set aside for later use, hopefully allowing for telecontrol and accessories in the future.

  8.1. Recommendations

For general use, it is recommended that:

- The driver does not exceed 77lbs [6]
- The car avoids liquid
- The car is not driven in the rain
- The car avoids sharp drops offs like curbs
  8.2. Recommended next steps

Firstly, the telecontrol should be reattached. This feature was initially implemented into the car for safety, but the snow munchers did not have time to fully integrate this. To re-implement this feature, a second PCB would have to be printed to allow for toggleable control between the IBT-2 motor drivers and the standard relay. This could be done most simplistically with 4 transistors for each motor. Two to allow for flow from the telecontrol relay and the other two to allow for flow from the joystick. The second reintegration should be rewiring the lights. The old lights are already attached and ready to run, however they need to be wired to a new power to turn on with the car. Similarly, the sound system can be easily repaired; however, the old speaker was damaged when removed, so a replacement would need to be purchased and reinstalled inside the dashboard.

9. References

[1] Kennedy Krieger Institute, “Go Baby Go: Mobility with Ride-On Cars,” Kennedy Krieger Institute, 2016. Accessed: Apr. 29, 2026. [Online]. Available: https://www.kennedykrieger.org/stories/potential-magazine/winter-2016/go-baby-go-mobility-with-ride-on-cars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,cars%20for%20their%20children's%20use%20at%20home

[2] University of Connecticut, “Go Baby Go Provides Modified Cars for Children with Disabilities,” UConn Today, Apr. 2025. Accessed: Apr. 29, 2026. [Online]. Available: https://today.uconn.edu/2025/04/go-baby-go-provides-modified-cars-for-children-with-disabilities/

[3] Instructables, “GoBabyGo: Make a Joystick-Controlled Ride-On Car,” Instructables. Accessed: Apr. 29, 2026. [Online]. Available: https://www.instructables.com/GoBabyGo-Make-a-Joystick-controlled-Ride-on-Car/

[4] Elsevier, “555 Timer,” ScienceDirect Topics. Accessed: Apr. 29, 2026. [Online]. Available: https://www.sciencedirect.com/topics/engineering/555-timer

[5] Ø. Moseng, “555 Timer,” Build Electronic Circuits. Accessed: Apr. 29, 2026. [Online]. Available: https://www.build-electronic-circuits.com/555-timer/

[6] BCP, SKY907 User Manual. Accessed: Apr. 29, 2026. [Online]. Available: https://www.manualslib.com/manual/1315772/Bcp-Sky907.html?page=3#manual

10. Appendices

APPENDIX A – Child using” GoBabyGo!” car where there is a button on the steering wheel.

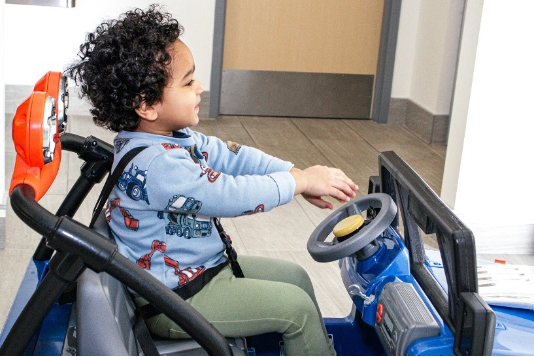
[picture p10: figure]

APPENDIX B - Picture of an existing solution from “Autodesk” and their joystick-controlled car.

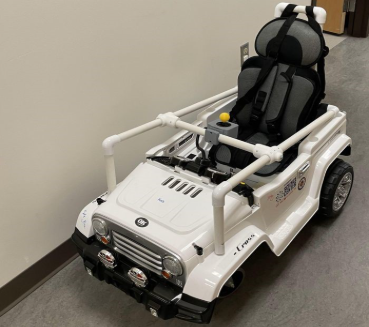
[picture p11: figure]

APPENDIX C – Block Diagram of the car’s circuit.

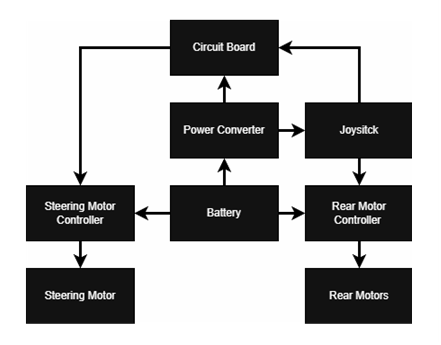
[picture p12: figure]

APPENDIX D – Internal switching logic of the arcade joystick.

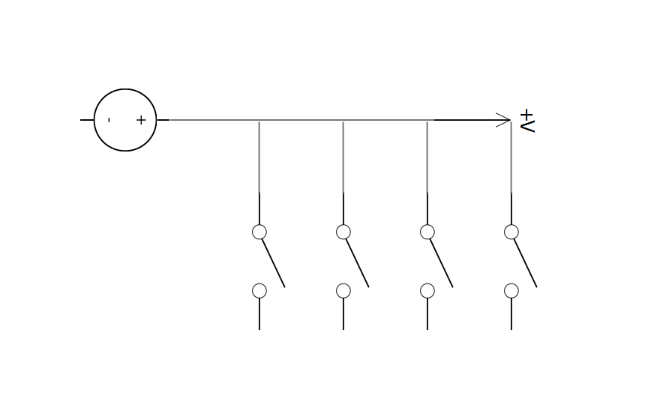
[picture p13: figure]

APPENDIX E – SolidWorks drawing of the joystick mount.

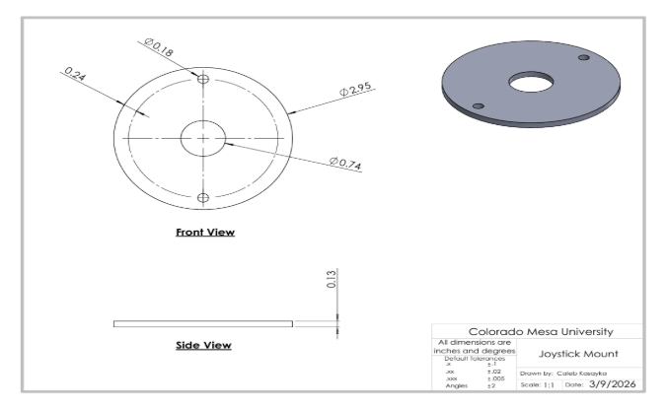
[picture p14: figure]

APPENDIX F – Function diagram of an H-Bridge Controller.

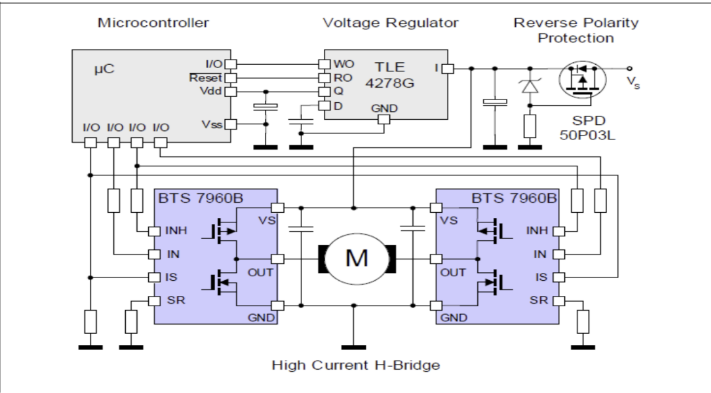
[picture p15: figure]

APPENDIX G – Diagram of a 555 timer and the respective pins.


APPENDIX H – The circuit diagram of a pulse shaping module.

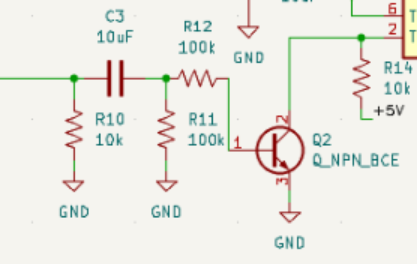
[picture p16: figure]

APPENDIX I – Image of the printed circuit board including 555 timers & the pulse shaping module.

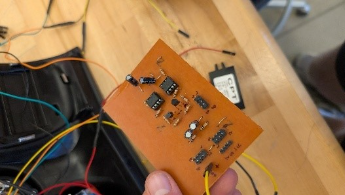
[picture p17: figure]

APPENDIX J – Table of bill of materials & cost estimate for the project.

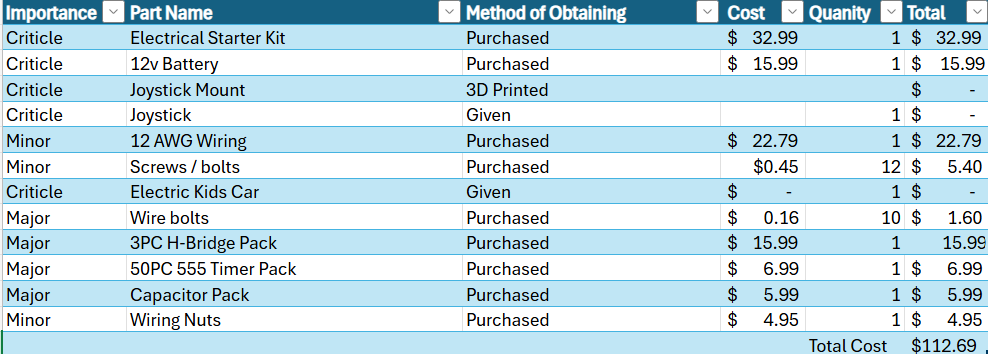
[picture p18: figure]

APPENDIX K – Gantt chart of task deadlines.

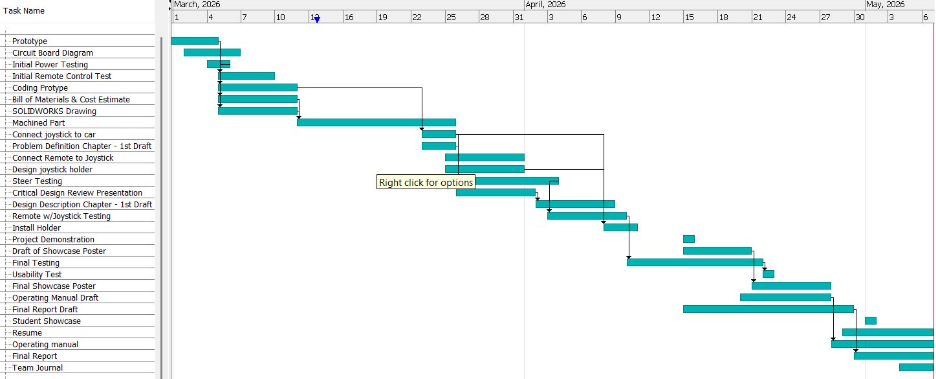
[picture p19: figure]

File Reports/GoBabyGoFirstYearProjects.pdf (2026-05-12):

# Go Baby Go

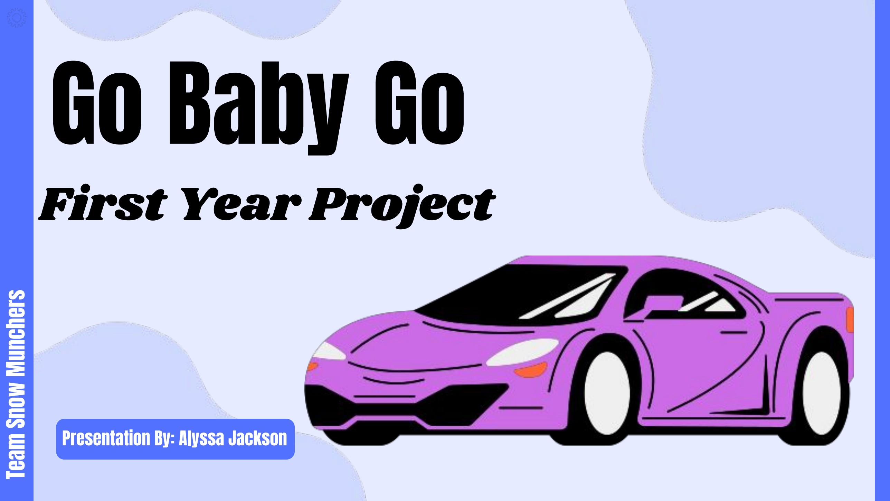
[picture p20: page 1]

# Team Snow Munchers

# First Year Project

# Presentation By: Alyssa Jackson

# TABLE OF Contents

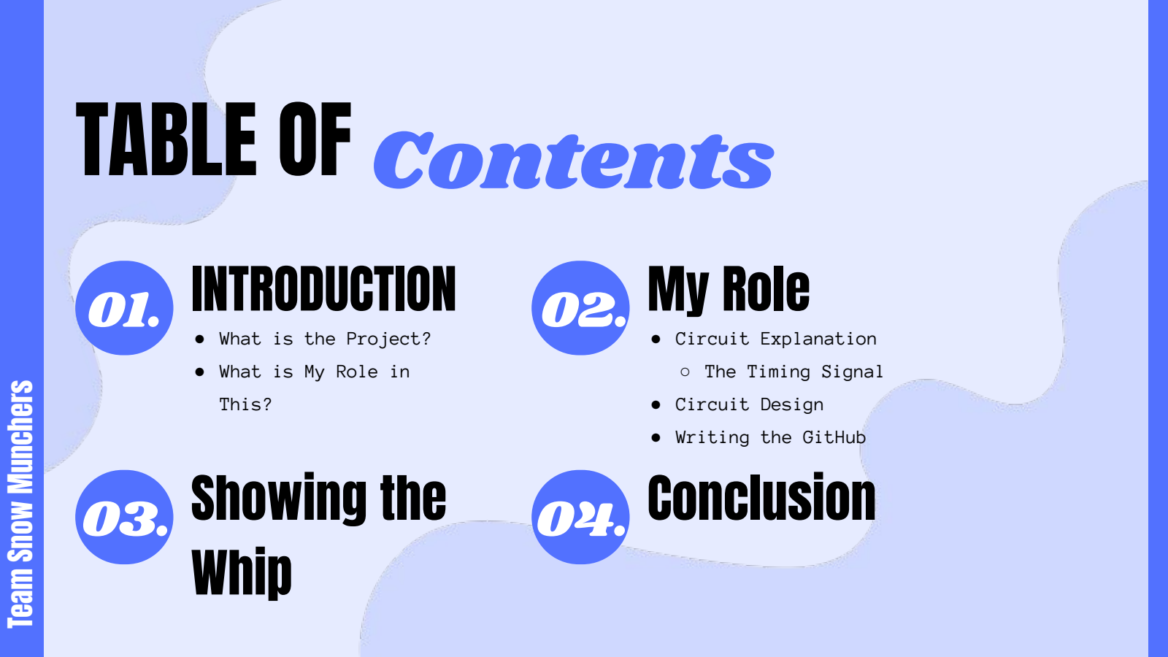
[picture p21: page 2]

# . INTRODUCTION

# . Showing the

| Whip

# My Role

# Conclusion

- What is the Project?
- What is My Role in
This?
- Circuit Explanation
- The Timing Signal
- Circuit Design
- Writing the GitHub

# Team Snow Munchers

# . INTRODUCTION

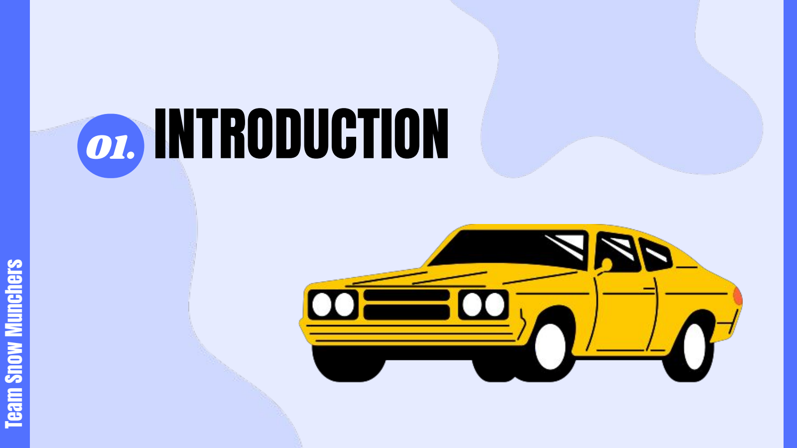
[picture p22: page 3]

# Team Snow Munchers

# What is

# the Project?

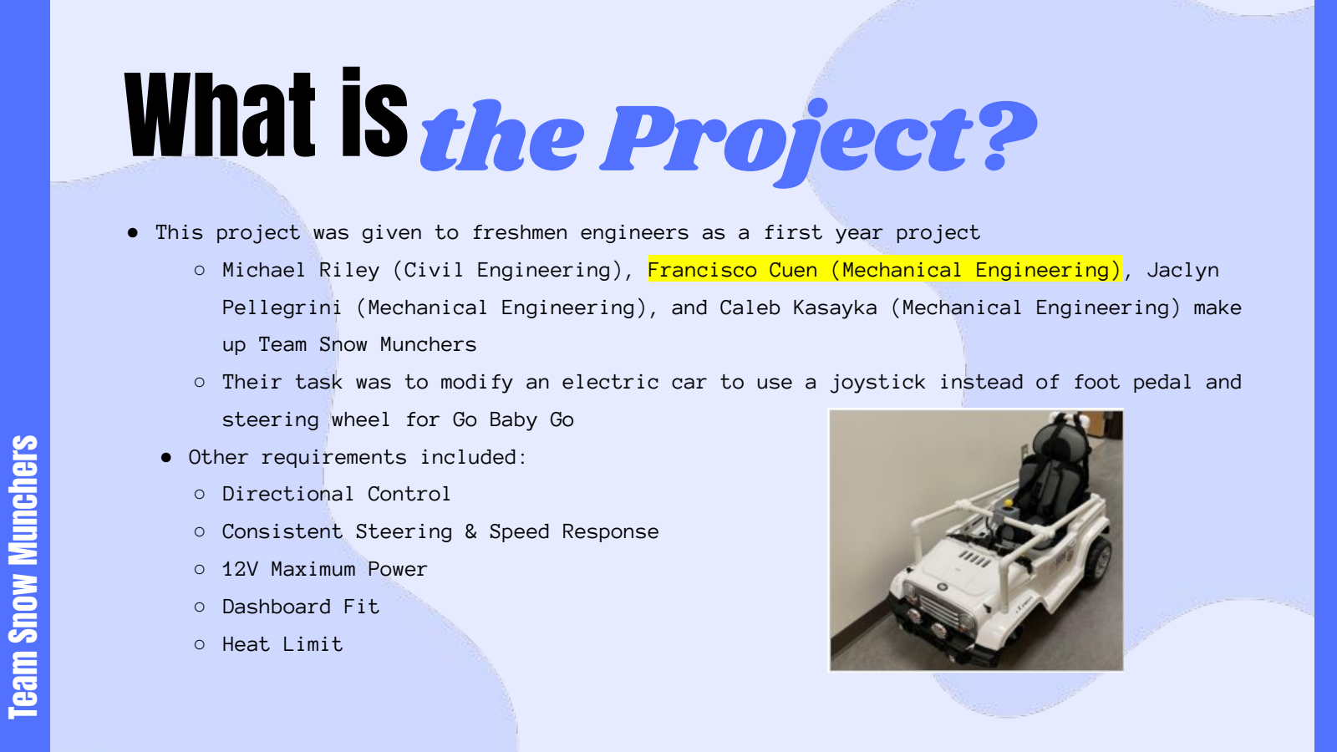
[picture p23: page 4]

- This project was given to freshmen engineers as a first year project
- Michael Riley (Civil Engineering), | Francisco Cuen (Mechanical Engineering), Jaclyn
Pellegrini (Mechanical Engineering), and Caleb | Kasayka (Mechanical Engineering) make
up Team Snow Munchers
- Their task was to modify an electric car to use a joystick instead of foot pedal and steering wheel for Go Baby Go
- Other requirements included:
- Directional Control
- Consistent Steering & Speed Response
- 12V Maximum Power
- Dashboard Fit
- Heat Limit

# Team Snow Munchers

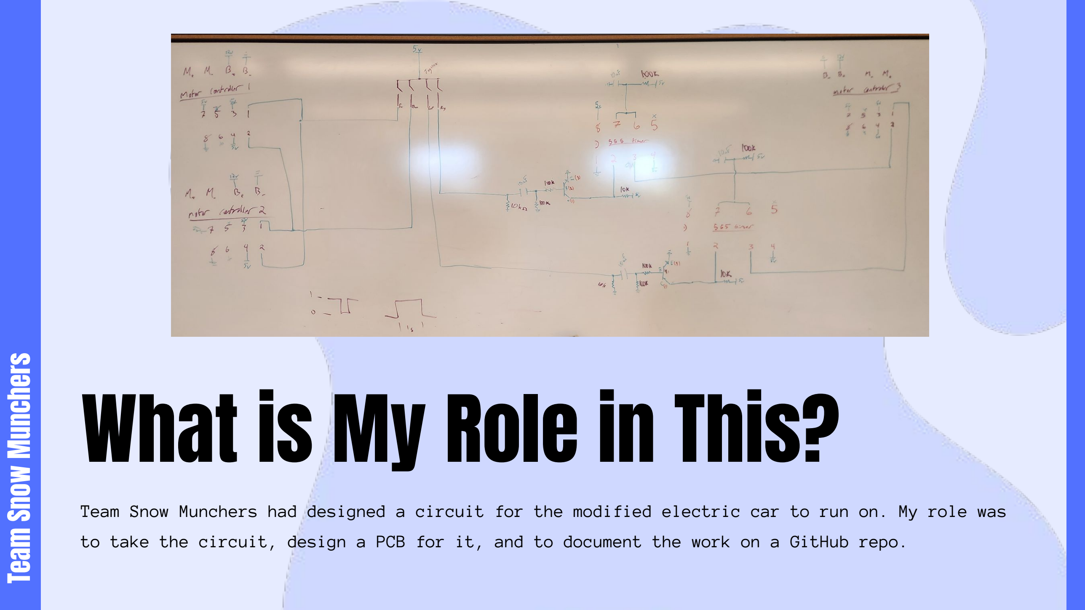
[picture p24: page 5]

# Team Snow Munchers What is My Role in This?

Team Snow Munchers had designed a circuit for the modified electric car to run on. My role was to take the circuit, design a PCB for it, and to document the work on a GitHub repo.

# . My Role

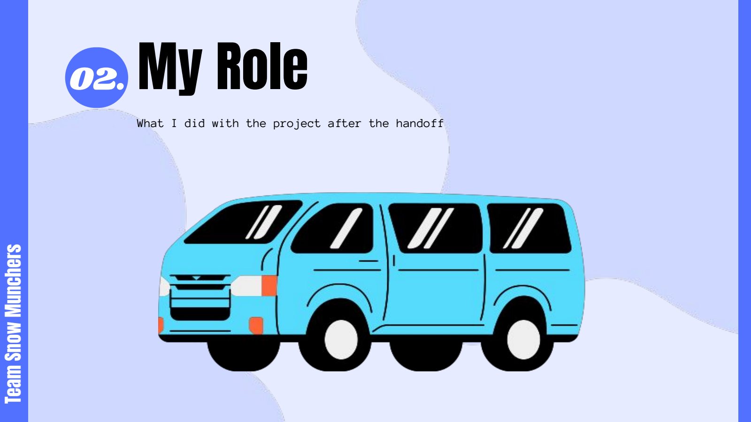
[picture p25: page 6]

# Team Snow Munchers

What I did with the project after the handoff

# Circuit

# Explanation

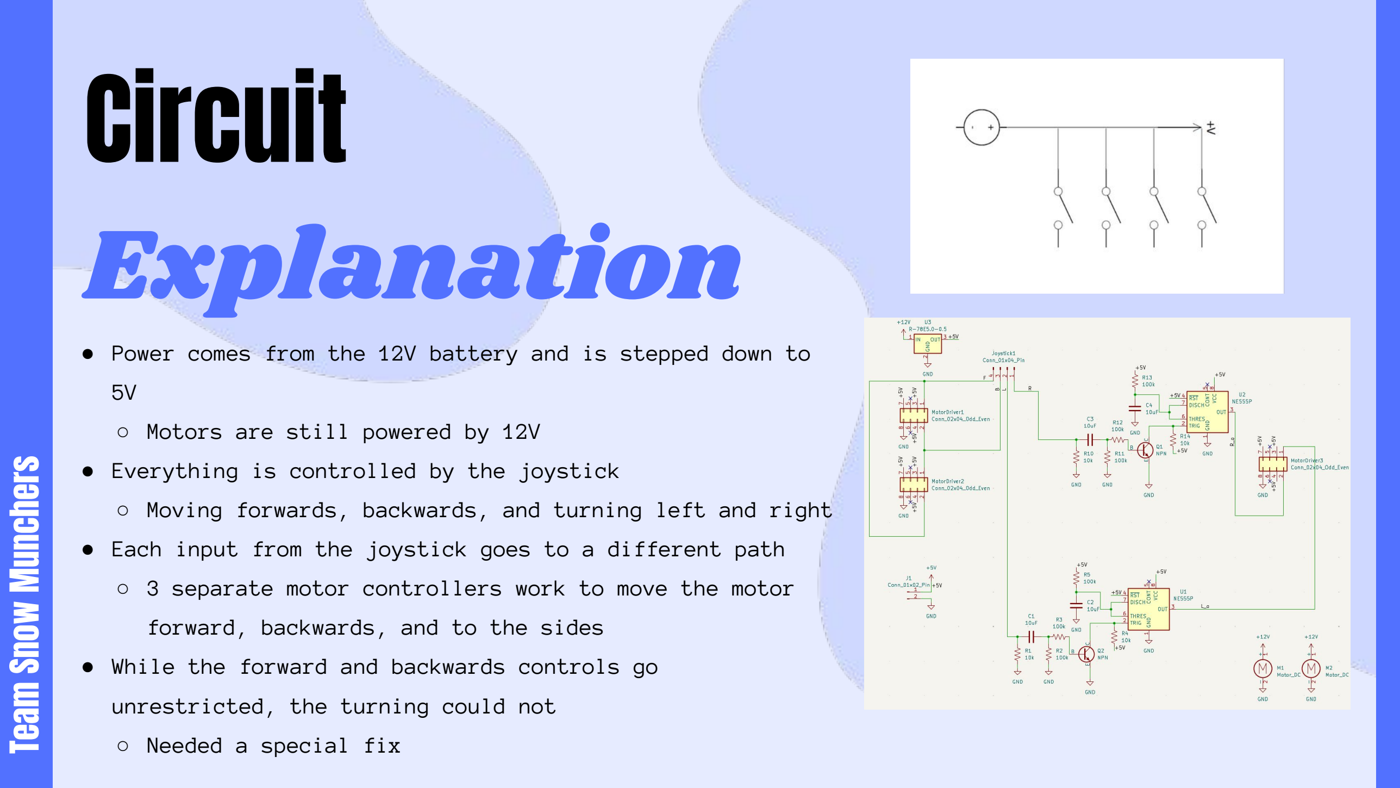
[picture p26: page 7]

# Team Snow Munchers

- Power comes from the 12V battery and is stepped down to 5V
- Motors are still powered by 12V
- Everything is controlled by the joystick
- Moving forwards, backwards, and turning left and right
- Each input from the joystick goes to a different path
- 3 separate motor controllers work to move the motor forward, backwards, and to the sides
- While the forward and backwards controls go unrestricted, the turning could not
- Needed a special fix

# The

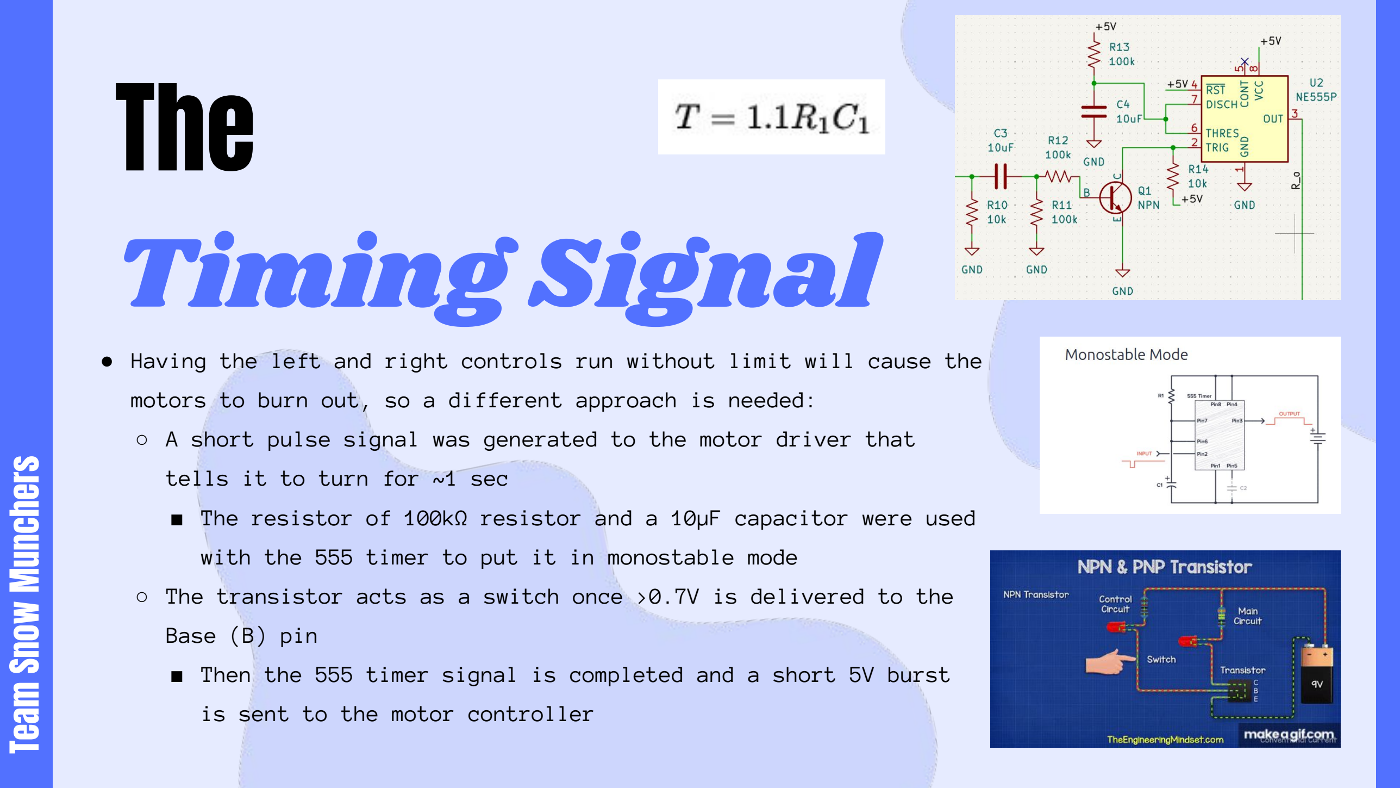
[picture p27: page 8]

# Team Snow Munchers

- Having the left and right controls run without limit will cause the motors to burn out, so a different approach is needed:
- A short pulse signal was generated to the motor driver that tells it to turn for ~1 sec
■ The resistor of 100kΩ resistor and a 10µF capacitor were used with the 555 timer to put it in monostable mode
- The transistor acts as a switch once >0.7V is delivered to the Base (B) pin
■ Then the 555 timer signal is completed and a short 5V burst is sent to the motor controller

# Timing Signal

# Circuit

# Design

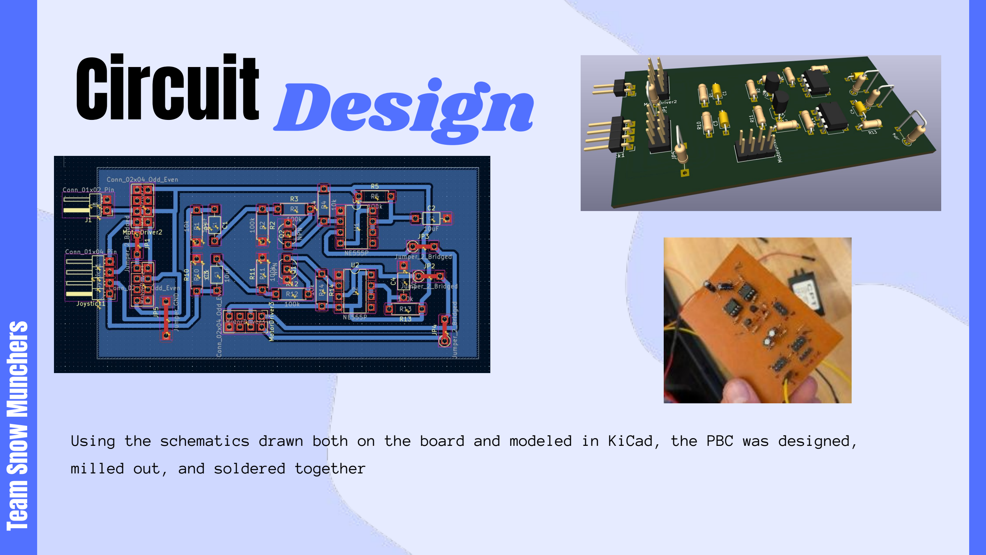
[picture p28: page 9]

# Team Snow Munchers

Using the schematics drawn both on the board and modeled in KiCad, the PBC was designed, milled out, and soldered together

# Writing the

# GitHub

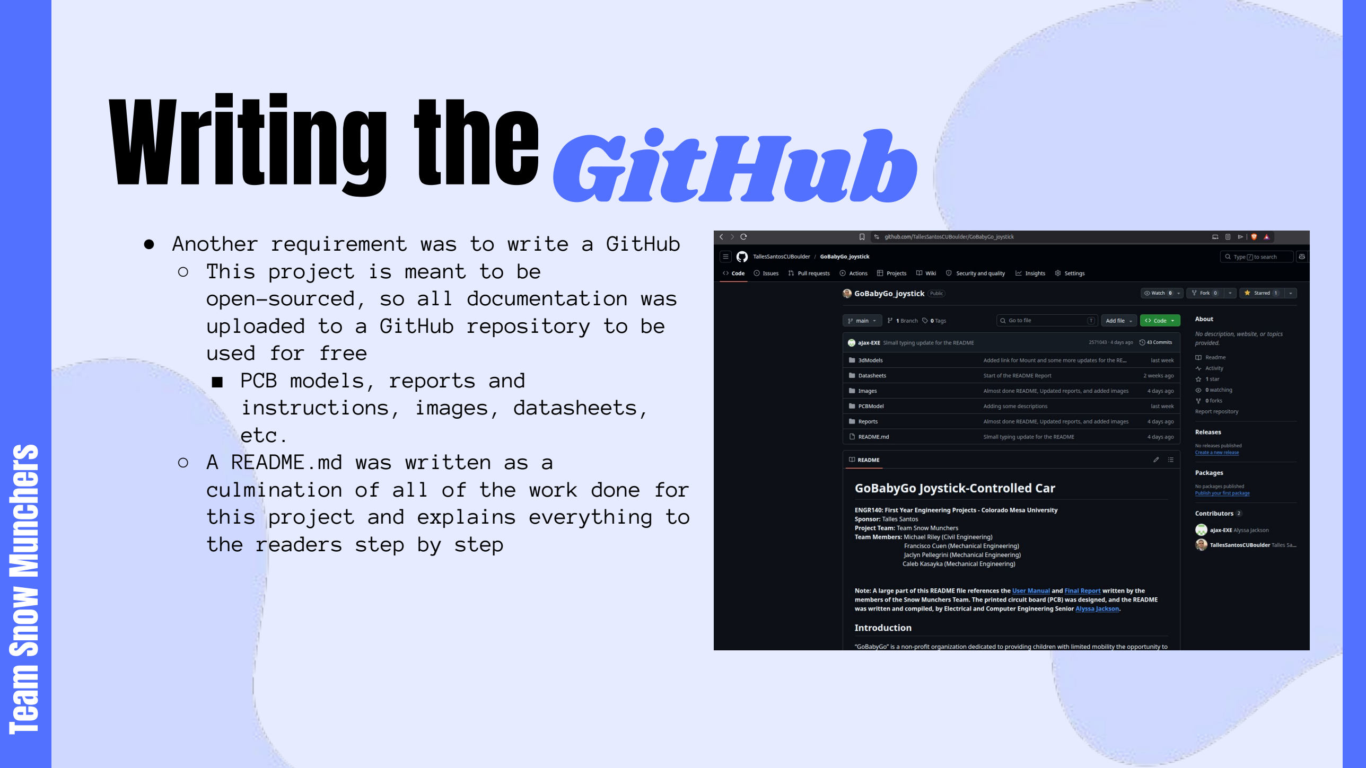
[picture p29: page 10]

# Team Snow Munchers

- Another requirement was to write a GitHub
- This project is meant to be open-sourced, so all documentation was uploaded to a GitHub repository to be used for free
■ PCB models, reports and
instructions, images, datasheets, etc.
- A README.md was written as a culmination of all of the work done for this project and explains everything to the readers step by step

Showing the Whip .

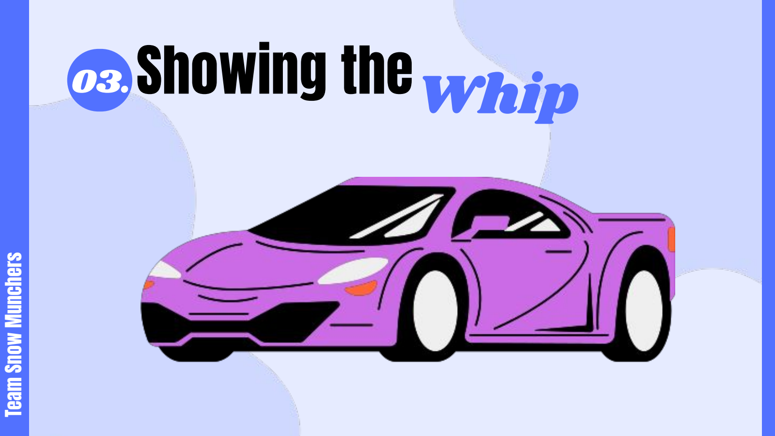
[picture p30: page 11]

# Team Snow Munchers

# Conclusions

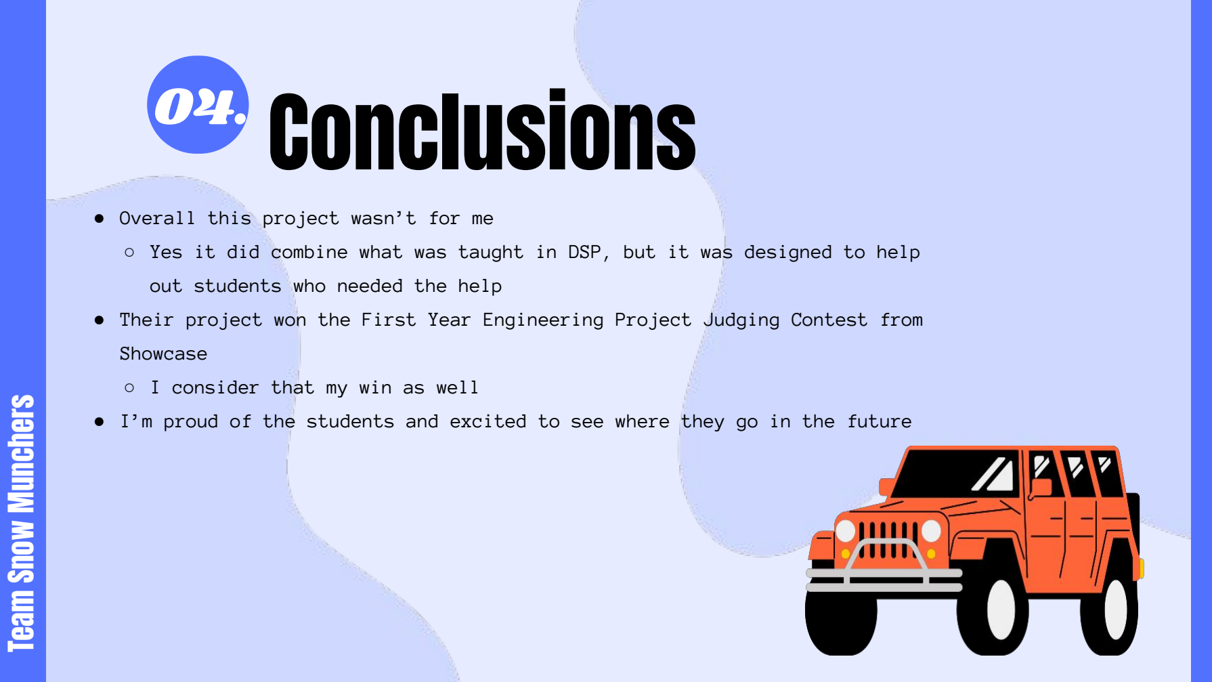
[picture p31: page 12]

# Team Snow Munchers

- Overall this project wasn’t for | me
- Yes it did combine what was taught in | DSP, but it was designed to help
out students who needed the help
- Their project won the First Year Engineering Project Judging Contest from Showcase
- I consider that my win as well
- I’m proud of the students and excited to see where they go in the future

# THANK YOU!

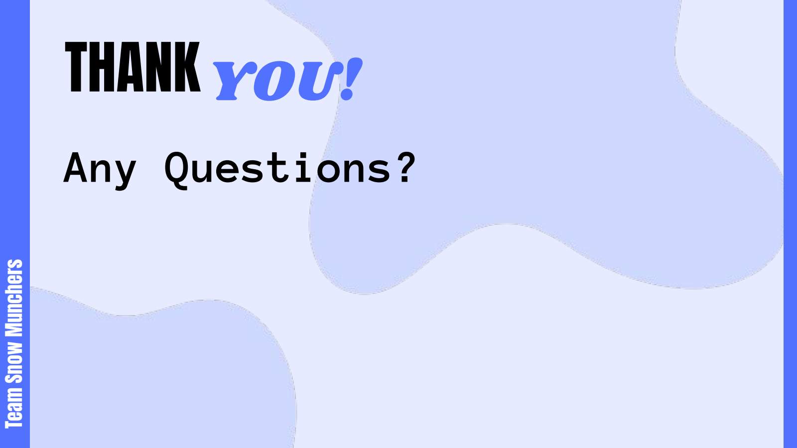
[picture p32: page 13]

# Team Snow Munchers

# Any Questions?

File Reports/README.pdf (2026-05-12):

# GoBabyGo Joystick-Controlled Car

ENGR140: First Year Engineering Projects - Colorado Mesa University

Sponsor: Talles Santos

Project Team: Team Snow Munchers

Team Members: Michael Riley (Civil Engineering)

Francisco Cuen (Mechanical Engineering)

Jaclyn Pellegrini (Mechanical Engineering)

Caleb Kasayka (Mechanical Engineering)

Note: A large part of this README file references the User Manual and Final Report written by the

members of the Snow Munchers Team. The printed circuit board (PCB) was designed, and the README

was written and compiled, by Electrical and Computer Engineering Senior Alyssa Jackson. (https://github.com/aJax-EXE)

## Introduction

“GoBabyGo” is a non-profit organization dedicated to providing children with limited mobility the

opportunity to play independently by adapting motorized toy cars. Many children with mobility challenges

struggle to press the pedal and steer simultaneously, making it difficult to operate the vehicle without

constant assistance. Typical “GoBabyGo” modifications reroute the pedal wiring to a button mounted on the

steering wheel, simplifying acceleration and improving usability.

After multiple iterations, the final design operated successfully and remained within budget. It reliably

controlled forward/backward motion and steering, and testing showed consistent performance with

minimal drift. The system was safe, intuitive, and easy for children to use. Future work should focus on

simplifying the steering circuit and adapting the design for broader use across different ride‑on car models

to benefit more children.


### A standin image of the completed modified car

## Project Overview

While the standard modifications help many children, some still find it difficult to press a button and steer at

the same time. This project aims to create a more intuitive control system by replacing both the pedal and

README.md | 2026-05-12

1 / 13 steering wheel with a single joystick. The joystick must control forward and backward motion as well as left

and right steering, operate safely under 12 V and 3 A, and be implemented for under $200.

### Design Requirements

Along with the functions that the car needs to reach from the the project overview, the following and

specific requirements were needed:

Directional Control

Provide forward, reverse, left, and right motion; each direction successfully actuates correct

motor behavior 10/10 trials with a response rate of .5 seconds.

Consistent Steering & Speed Response

Vehicle follows the same path in 5 repeated trials within acceptable tolerance (e.g., ±6 inches

lateral drift over 10-15ft).

12V Maximum Power

Must not exceed 12V thought out the electrical system.

Dashboard Fit

Total joystick assembly dimensions must not exceed 2.75 in (height) × 3.125 in (width). Zero

interference points and no natural obstructions.

Heat Limit

Must not exceed 113° over 15 minute time intervals.

### Electrical Solutions

For this car, a modification was made for the movement. Using a joystick instead of a steering wheel and

foot-powered pedals, the car can move forwards and backwards without restrictions, but turning left and

right is altered. Instead of turning left and right without restriction, moving or holding the joystick in either

direction causes the car to turn for only a set amount of time before stopping and waiting for another input.

This is to help keep the motors from stalling as ... ? (Include a video/gif of the car moving in all four

directions with the joystick)

2 / 13

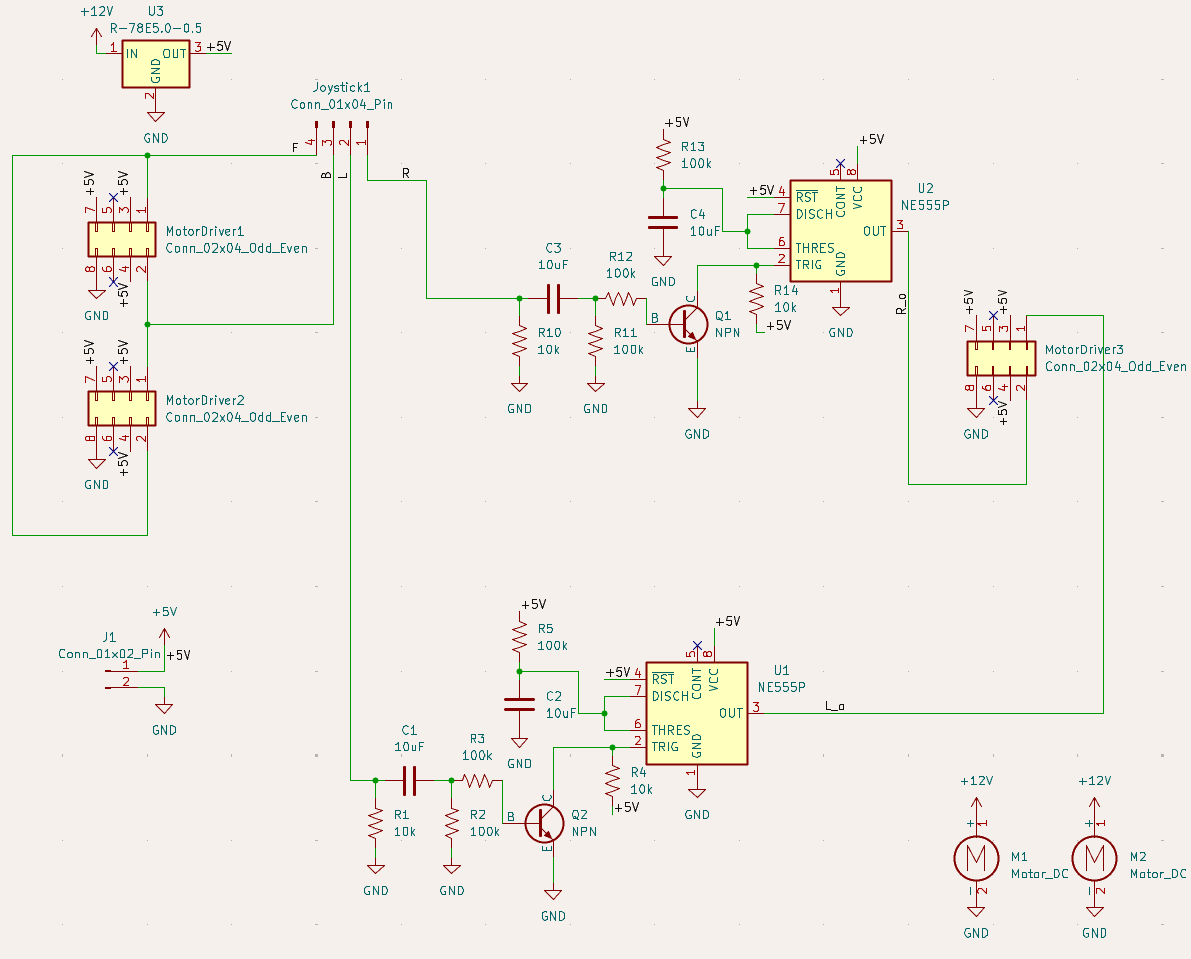
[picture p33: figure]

### The Full Circuit Diagram of the car

The full construction of the circuit requires the following components:

3 IBT-2 BTS7960 High Current H-Bridge Motor Drivers

3 / 13


### The Function diagram of an H-Bridge Controller

Full representation of the function of an H-Bridge Controller can be found in the above image.

When an input is received, it sends a signal to the H-bridge motor controller which recognizes

the voltage as a directional input and then outputs that signal into the motor itself. This allows

for safe, effective, bi-directional movement. The H-bridge has a total of 12 attachment points.

two for power in, two for power to motor, two for input detection (seen as “IN”), two for

inhibiting direction (“INH”, two for ISs), a ground for the logic board (GND), and a 5.5V input for

the logic board (“VCC”). This design will take advantage of all the inputs / outputs except for the

SIs.

2 LM555 Timer Chips


### Diagram of a 555 timer and the respective pins

A 555 timer is an integrated circuit that takes an electrical input and outputs a pulse over a

certain interval of time. This component is needed to turn the front steering motor to a certain

point so that the motor doesn’t overturn the mechanical component, breaking the car, and

4 / 13 burning out the motor. Power is inputted through the VCC pin which powers the circuit (as seen

in the above image). When a signal comes through the Trigger pin, it goes through the circuit

within the 555 and then a capacitor and resistor attached to the discharge and threshold pins

which controls how long a pulse is sent out of the output pin. For this project, the 555 is

operated in monostable mode, meaning it sends out a singular pulse and then returns to its

original state. To get the pulse to last for a certain time, the equation T=1.1RC where T is time, R

is the strength of the resistor, and C is the value of the capacitor. For the motor a 1 second pulse

is needed so values of a100kΩ resistor and a 10µF capacitor are needed.

A Joystick


### Internal switching logic of the arcade joystick

The above image illustrates the internal switching logic of the joystick. The joystick has five

wires with a gauge of 23 AWG (American Wire Gauge). These wires are connected to a circuit

board via a connector. This system consists of four signal wires, each for a different switch that

is also connected to the circuit board. The last wire serves as a 5V-12V source wire; the input

(5V-12V) will flow through this wire and in return, will output through one of the four switches

(possibly two) depending on which switch is compressed or activated.

An RC Car

For this project an existing car was bought and provided to the group, but the car model used

costs around $250 USD.

2 NPN Bipolar Junction Transistors

5 / 13


### The circuit diagram of the pulse shaping module used in the car


### The 3D Model that represents what the working model looks like

The transistors are the necessary part of the timing circuit. For the 555 to properly work, it

needs sharp, high input. This is not as simple as it would seem because our joystick is mainly

used in a “toggle” sense, where the driver will hold it left to turn left. After some testing, we

realized that this toggled system would lead to the output of the 555 system always being held

high. To fix this, we implemented what is called a pulse shaping module. This consists mainly of

a capacitor momentarily allowing a transistor to drain a power source to ground, creating a

quick pulse of electricity that the 555 timers can properly understand. The above images shows

6 / 13 the pulse shaping module implemented into the design of the circuit and the 3D model of the

completed PCB with all of its components.

Joystick Mount


### The SolidWorks drawing of the joystick mount

The joystick already has two existing mounting holes, 0.278 inches in diameter, implemented

into the factory design. With this, a CAD drawing was produced and integrated with these

existing holes (see Appendix E). The design functions similar to a washer where it will mount on

the original steering wheel location. Two bolts will run through the top (the side where the

joystick extrudes), and below there will be two nuts securing the simple assembly in place. The

above image consists of a SolidWorks drawing of the mount.

A 12V to 5V Voltage Step Down

Must be able to handle 3A of current and 15W of power.

6 100k Ohm Resistors

4 10k Ohm Resistors

4 10uF Capacitors

A 12V Battery

The model of car used includes a 12V 7AH battery. Most electric kid cars run on 6V, but this

system is designed for 12V. To use this system with a 6V battery, a voltage step down that goes

from 6V to 5V, or rather a simple voltage divider, needs to be used to run the system properly.

2 Rolls of 20 AWG Wire

One red and one black preferred.

Female to Female Jumper wires

The circuit starts at the battery going into the two gearboxed motors of the car and the voltage step down.

The 5V from the stepdown powers the rest of the system: all three of the motor drivers and the two 555

7 / 13 timer circuits. While the forward and backwards motor drivers are only activated with the direct signal from

the joystick, the left and right one first goes through there respective timing circuit to give the proper timed

signal.


### The Full PCB model for the car

The PCB holds the resistors, capacitors, and transistors that make up the timing circuit, as well as all of the

connectors necessary for both powering the board, connecting the joystick to the motor drivers, and for the

motor drivers themselves.

## Hardware Setup and How to Operate

For the complete instructions on how to modify the car to replicate the project, perform maintainence, and

for a full list of tools needed and how to use, refer to the User Manual written by the Snow Munchers.

### Recommendations for Operation

Before general use, it is recommended that:

The driver does not exceed 77lbs

The car avoids liquid

The car is not driven in the rain

The car avoids sharp drops offs like curbs

## Results

Overview

The electric ride on car was evaluated against the specified design requirements through structed user

testing and system performance checks. Each criterion, directional control, steering consistency, power limit,

heat limit, and size requirement, was assessed during real world operation to ensure the design met both

functional and safety expectations. Users operated the vehicle under normal conditions, allowing the team

8 / 13 to observe control, responsiveness, and overall usability. The system was required to satisfy all evaluation

criteria in order to be considered successful. Testing results showed that the ride on car met all the design

requirements, demonstrating reliable performance, safe operations, and suitability for its intended use.

CRITERIA 1 – DIRECTIONAL CONTROL

Provide forward, reverse, left, and right motion; each direction successfully actuates correct motor behavior

10/10 trials with a response rate of .5 seconds.

PURPOSE OF EVALUATION: The purpose of the directional control test is to ensure that the electric

ride on car responds accurately and reliably to user inputs. Effective directional control is essential for

safe operations, as it allows the user to intentionally move the vehicle forward, backward, and

laterally, ensuring the car can be maneuvered smoothly during normal operation and while navigating

obstacles or turns.

TESTING METHODS: The evaluation of this design criteria requires that the user manually push the

joystick in each direction, forward, backward, left, and right. This was tested in two ways, a static test,

elevating the car off a flat surface so that the wheels can spin freely allowing the testers to visually

see the steering response. And a dynamic test, driving the car through a specially crafted course

designed with turns and corners to test the steering compacity while in motion. For the setup, the car

was supported above a flat surface using four wooden 2 by 4 blocks, ensuring that all the wheels were

fully suspended and unrestricted in rotation. This configuration eliminated ground friction and

external load effects. Allowing isolated evaluation of the motor and steering response. With the

vehicle secured, the joystick was actuated individually in the forward, reverse, left, and right

directions. Observations were made to confirm correct wheel rotation direction, steering actuation,

and immediate system response corresponding to each input. Any unintended motion, delay, or

incorrect direction would indicate a fault in the signal interpretation or motor control. For the dynamic

control test the electric ride on car was operated on a flat indoor surface and driven through a

predefined course designed to replicate realistic operating conditions. The course consisted of

straight sections, gradual turns, and sharp corners. Requiring continuous directional input

adjustments. The user controlled the vehicle solely via the joystick, executing directional changes

while the car remained in motion. This test evaluated the system’s ability to interpret joystick input

under load, maintain control during directional transitions, and execute smooth turning without loss

of stability or responsiveness.

RESULTS & DISCUSSION: The electric ride on car demonstrated correct directional response during

both static and dynamic testing. In the static response test, joystick inputs in all four directions

resulted in correct wheel movement with no observed latency, incorrect rotation, or unintended

behavior. During the dynamic testing, the vehicle successfully followed the predetermined course and

executed directional changes while in motion. The system maintained full responsiveness and

directional accuracy thought out all test runs. No failures or loss of control were observed. As a result,

the directional control system achieved a 100% success rate across all tests. The results indicated that

the directional control system functions as intended under both unloaded and operational conditions.

The static test confirmed control signal interpretation and motor actuation, while the dynamic test

verified reliable performance under load. Although quantitative data was not collected, consistent

qualitative performance across multiple trials demonstrates that the system meets the directional

control requirements. The ability to maintain accurate direction changes while motion indicates

9 / 13 sufficient control logic, motor response, and system integration. Therefore, the direction control

design requirement was fully satisfied.

CRITERIA 2 – STEERING CONSISTENCY

Vehicle follows the same path in 5 repeated trials within acceptable tolerance (e.g., ±6 inches lateral drift

over 10-15ft).

PURPOSE OF EVALUATION: The purpose of the steering consistency requirement is to ensure that

the vehicle responds predictably and repeatably and repeatably to identical steering inputs.

Consistent steering behavior is essential for user confidence, safe operation, and accurate

maneuvering. This requirement verifies that the steering system produces uniform turning behavior

without variation or drift during repeated use.

TESTING METHODS: Steering consistency was assessed using a straight-line deviation test. The

vehicle was commanded to drive forward with a fixed joystick input while lateral deviation from a

defined centerline was measured. The test evaluates the vehicle’s ability to maintain a straight

trajectory under constant input. This method demonstrates whether the steering system produces

predictable and repeatable behavior, which directly impacts controllability and user confidence in the

finished product. For the setup, the steering consistency test was conducted on a flat, level surface to

minimize external influences. A straight reference line was established using a tape measure at a fixed

distance placed longitudinally along the test path. The electric ride on was aligned so that its

centerline coincided with the reference line at the starting position. The vehicle was positioned at a

consistent starting distance for each trial to ensure repeatability. During testing, the car was allowed

to travel forward along the reference line while lateral deviation from the centerline was visually

monitored and measured relative to the ruler. All tests were performed under identical surface and

environment conditions to ensure consistent results.

RESULTS & DISCUSSION: The straight-line steering consistency test produced lateral drift across

multiple trials and test length ranging from approximately 10 – 15ft. measured drift values varied

significantly between trials, indicating nonuniform steering behavior under constant joystick input.

Server trials remained within the ±6 in acceptance tolerance, deviations were small and showed no

progressive drift over the test distance. However few outliers appeared in the tests but they were

ruled out for being user error and were taken note of but not deemed important to the over all trials.

Within this acceptance range, deviations were small and showed no progressive drift over the test

distance. The compliant data demonstrates repeatable straight line tracking performance under

consistent input conditions. The in tolerance results indicate that the steering system is capable of

maintaining an acceptably straight trajectory when commanded with fixed forward input. The limited

magnitude of lateral deviation suggests that the mechanical steering alignment and control response

are sufficient for stable, predictable operation in the finished design. These results support the

conclusion that, within defined performance limits, the steering system meets the consistency

requirement. Maintaining deviation with ±6 inches ensures adequate controllability and user

confidence during straight line motion.

CRITERIA 3 – POWER LIMIT

Must not exceed 12V thought out the electrical system.

10 / 13

PURPOSE OF EVALUATION: The purpose of the power limit requirement is to ensure that the electric

ride on car operates within safe electric and mechanical limits. Restricted power output prevents

excessive speed, reduces stress on system components such as the motor, battery, and drivetrain, and

minimizes potential safety risks to the user. This requirement ensures controlled performance while

maintaining reliability and compliance with design constraints for the finished project.

TESTING METHODS: To test, the power limit requirement was evaluated by measuring electrical

current and voltage at key point throughout the vehicles electrical system. A multimeter was used to

monitor voltage and current in selected wiring segments supplying the motor and control electronics

during operation. Testing verified that system voltage remained below 12 V and that operating

current did not exceed the specified limit of a 3 amp under normal driving conditions. Measurements

were taken while the vehicle was powered and active to ensure compliance under realistic load

conditions. For the setup, power limit testing was conducted using a digital multimeter to measure

voltage and current at multiple points within the vehicle’s electrical system. Measurement locations

included the batter output, motor supply lines, and control circuit wiring to capture representative

operating conditions. The car was powered on and operated under normal operating conditions while

the multimeter probes were connected in series for current measurement and in parallel for voltage

measurement. Tests were performed while the vehicle was stationary and during motion to account

for load variation. All measurements were taken with the system fully assembled to reflect real

operating conditions.

RESULTS & DISCUSSION: Power limit testing confirmed that the electrical system operated within the

defined constraints during all the testing conditions. Measured system voltage remained below the

maximum allowable limit of 12V, and operating current did not exceed 3 amps at any monitored

location. All measurements points across the battery, motor supply, and control wiring remained

within the specified limits under both stationary and dynamic operating conditions, as a results, the

power limit requirements was successfully met for all tests. The results confirm that the electrical

power system operates within the specified voltage and current limits under normal operating

conditions. Maintaining voltage below 12 V and current at or below 3 amps ensures safe operation of

the motor and control electronics while reducing the risk of overheating, electrical stress, and

components failure. Compliance with the power limit requirement indicates that the selected

electrical components and system configuration are appropriately matched to the vehicle’s

performance needs. This controlled power outage contributes to overall system reliability and user

safety, supporting the suitability of the design for its intended application.

CRITERIA 4 – HEAT LIMIT

Must not exceed 113° over 15 minute time intervals.

PURPOSE OF EVALUATION: The purpose of the heat limit requirement is to ensure that the electrical

and mechanical components of the electric ride on car operate within safe temperature ranges during

normal use. Limiting heat buildup prevents thermal damage, reduced the risk of components failure,

ensures user safety. This requirements supports system reliability longevity and consistent

performance throughout operation.

TESTING METHODS: The heat limit requirement was evaluated by monitoring temperature during

sustained operation. An Arduino based temperature sensing system was connected to the motor to

continuously monitor thermal performance. The motor was operated continuously for a duration of

11 / 13

15 minutes under normal operating conditions. Temperature readings were observed to determine

whether the motor temperature remained below the maximum allowable limit of 113 °F throughout

the test period. For the setup, the heat limit was conducted using an Arduino microcontroller

interfaced with a temperature sensor mounted directly to the motor casing to measure operating

temperature. The sensor was secured to ensure consistent thermal contact and accurate temperature

readings throughout the test. The electric ride on car was placed in a stationary configuration to allow

continuous motor operation without external interruptions. Power was supplied under normal

operating voltage, and the motors were run continuously for a 15 minute duration. Temperature

reading were monitored in real time through the Arduino system to verify that the motor temperature

remained below the maximum allowable limit of 113 °F for the entire test period.

RESULTS & DISCUSSION: The heat limit requirement was considered satisfied based on qualitative

observation during vehicle operation. Although a full 15 minute controlled temperature test was not

completed due to time constraints, the motor was operated during multiple system tests without

exhibiting signs of excessive heat build up. Though these test, the motor maintained stable

performance with no observable thermal degradation, shut down, or adverse response related to heat

generation. Based on the motors behavior during externed use and the absence of overheating

indicators, the system was determined to operate within acceptable thermal limits. Although a full

duration heat test was not completed, the observed system behavior during extended operations

indicted that the motor operates within acceptable thermal limits. The absence of thermal issues

during sustained use suggests that the selected motor and power configuration are sufficient for the

intended operating conditions. While additional quantitative temperature data would strengthen

validation, the qualitative results support the conclusion that the heat generation does not pose a

safety or reliability concern for the current design. Future testing with continuous temperature

logging over longer duration recommended to further validate thermal performance and confirm

compliance under all operating scenarios.

CRITERIA 5 – SIZE REQUIREMENT

Total joystick assembly dimensions must not exceed 2.75 in (height) × 3.125 in (width). Zero interference

points and no natural obstructions.

PURPOSE OF EVALUATION: The joystick components were required to fit within a designated

envelope of 2.75in x 3.125 in space to ensure proper integration with the vehicle. Maintaining this size

constraints prevents interference with vehicle operation, preserved drivability, and reduced the

likelihood of accidental contact or mechanical damage during regular use. A compact fit also supports

ergonomic accessibility for the user while allowing the control system to be securely mounted and

protected within the vehicle structure.

TESTING METHODS: Size evaluation was conducted through a physical fitment verification and user

interaction testing. The control circuit board was designed and assembled to conform to the allocated

dashboard of 2.75 in x 3.125 in. prior to permeant installation, the joystick components were

temporally secured in the location using tape to allow visual and dimensional comparison with he

available space. Once loosely secured, the vehicle was operated in a simulated use scenario. Testers

interacted with the ride on car as a child user would, ensuring that the joystick and associated

components did not obstruct operation, restrict movement, or practical useability of the installed

parts.

12 / 13

RESULTS & DISCUSSION: During size evaluation, the joystick mount component required four design

iterations due to improper fit within the allocated dashboard space. Each reprint addressed

dimensional and alignment issues until the final mount achieved a secure and accurate fit. The circuit

board and associated wiring were successfully integrated within the design rea and remained neatly

secured throughout testing. No components were exposed or positioned in a way that could be easily

accessed or damaged during normal use. Once fully installed, all components fit securely within the

available space without requiring further adjustment. These results confirm that the size requirement

was met in the final configuration. Safe security of critical control components ensures the physical

compatibly with the vehicle and is suitable for real-world use. Proper fitment directly affects

drivability, user interaction, and long-term durability. Particularly in a ride on device intended for child

use. Components that excess the allocated space or are improperly positioned introduce risks of

accidental contact, interference during operation, or mechanical damage over time. The testing

approach verifies dimensional compliance, simulating realistic user interaction. Supporting safe

operation and reinforcing the overall robustness of the design.

### Conclusion

The electric ride on car joystick integration designed by the Snow Munchers team wad successfully evaluated

against the defined design requirement using a combination of user testing, qualitative observation, and

targeted system checks. The vehicle demonstrated reliable directional control and acceptable steering

consistency under controlled testing conditions. Supporting predictable and safe maneuverability. Electric

testing confirmed operation within the specified power limits, ensuring system safety and component

reliability. Thermal performance did not present observable issues during extended operation, indicating the

heat generation remains within acceptable bounds for the intended use. Additionally, the control

components were successfully integrated within the allocated size constraints, preventing interference with

drivability and reducing the risk of damage during regular use. Indicating the final design meets the primary

functional, safety, and usability criteria created for the projects solid foundation and future refinement.

## Next Steps

Firstly, the telecontrol should be reattached. This feature was initially implemented into the car for safety,

but the snow munchers did not have time to fully integrate this. To re-implement this feature, a second PCB

would have to be printed to allow for toggleable control between the IBT-2 motor drivers and the standard

relay. This could be done most simplistically with 4 transistors for each motor. Two to allow for flow from the

telecontrol relay and the other two to allow for flow from the joystick. The second reintegration should be

rewiring the lights. The old lights are already attached and ready to run, however they need to be wired to a

new power to turn on with the car. Similarly, the sound system can be easily repaired; however, the old

speaker was damaged when removed, so a replacement would need to be purchased and reinstalled inside

the dashboard.

13 / 13

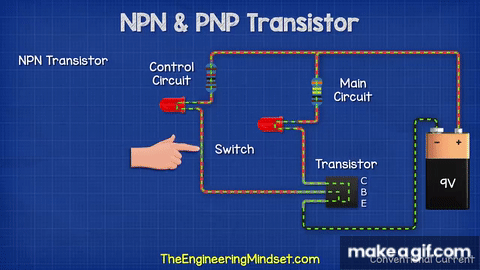
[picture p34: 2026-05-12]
Images/NPN_PNP_Transistors_explained_electronics_engineering.gif

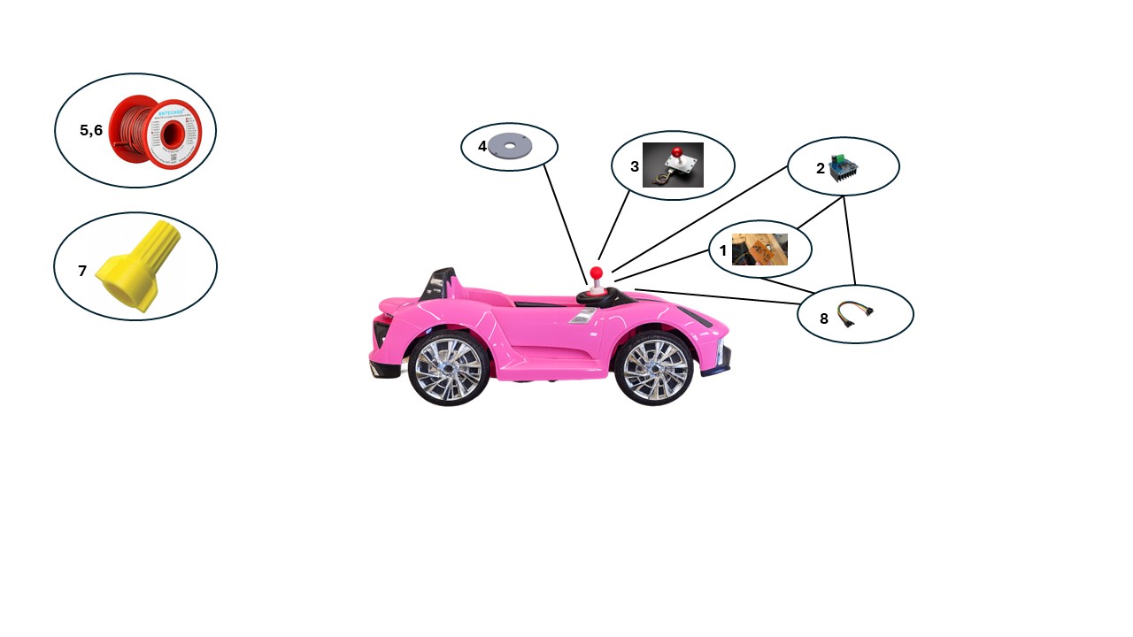
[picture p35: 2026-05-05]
Images/CarDiagram.jpg

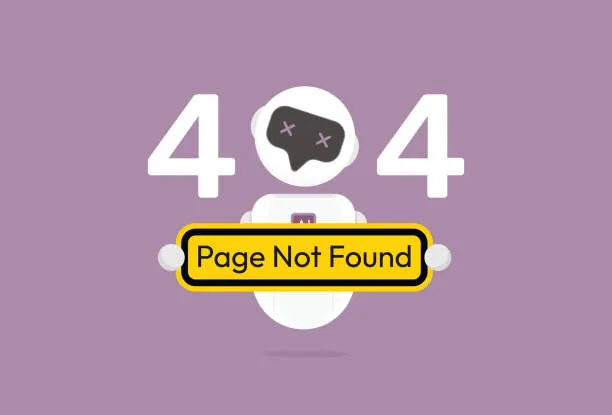
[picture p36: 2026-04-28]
Datasheets/PutLinkHere.webp

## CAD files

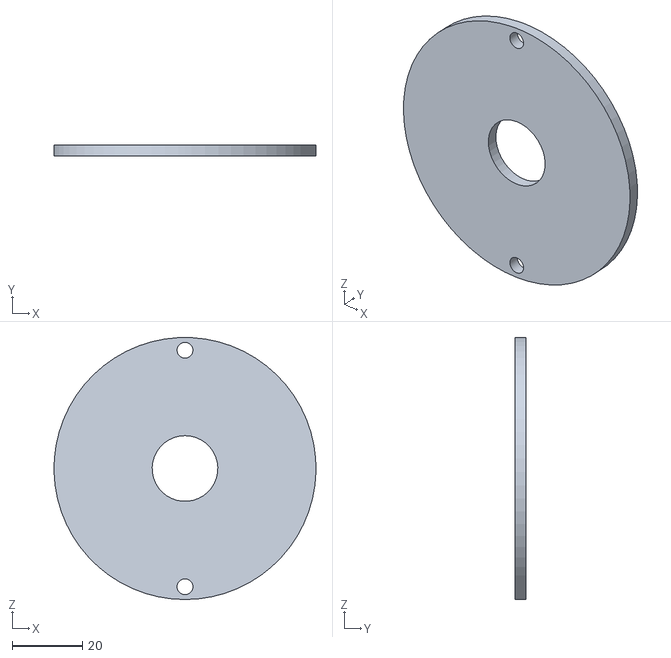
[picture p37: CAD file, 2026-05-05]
3dModels/Joystick Mount 3.STL
74.8 x 3.17 x 74.8

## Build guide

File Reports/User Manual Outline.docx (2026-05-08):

The Redesign of a Motorized Toy Car by Adapting the Throttle & Steering Controls to Engage Via a Joystick

User Manual & Guidelines

The Snow Munchers

April 26, 2026

### User Manual Outline

1. Table of Contents
2. Introduction – Pg. 1
  2.1. Scope
  2.2. Safety Warnings & General Guidelines Prior to Assembly
3. Package Contents – Pg. 3-4
  3.1. Figures 1-8 & Table of Labeled Packaged Contents
4. Materials & Tools Required – Pg. 4
  4.1. List of Tools Needed
5. Procedures for Assembly & Operation – Pg. 5-6
  5.1. Assembly
  5.2. Operation
6. Maintenance Guideline – Pg. 6
7. Storage Guideline – Pg. 7
8. Troubleshooting Guideline – Pg. 7
9. Technical Support – Pg. 7
10. Spare Sparts & Components – Pg. 8
2. Introduction
  2.1. Scope

This user manual contains guidelines for the installation of a joystick onto a “Bestchoiceproducts’ SKY908” children’s rechargeable toy car for adaptive use. This kit changes the manner of directional control of the car using a joystick, which replaces both the throttle pedal and steering wheel to allow children with limited mobility to operate the car intuitively and independently. After reading this manual, a knowledgeable adult should be able to assemble the system and allow children to operate it safely. This product was designed with the best intentions to help kids be kids.

  2.2. Safety Warnings & General Guidelines Prior to Assembly

Read this manual before assembling this product to understand proper operation, assembly, installation, troubleshooting, and safety concerns. This product must be assembled and installed by an adult with the proper tools and knowledge. It is important to avoid the elements from contacting any electrical components... no direct water or heat exposure. Please store this product in a cool, dry place to avoid the risk of damage to you, your children, and belongings.

Please be advised: YOU are modifying an existing product; the Snow Munchers are not liable for injuries caused by YOUR modifications. After implementing this product onto your existing car, the parental controls will NOT be operational... parental supervision is strongly advised for the participating child or children.

⚠ PLEASE NOTE THE WARNINGS INDICATED BY THIS SYMBOL: ⚠

3. Package Contents

This product comes with the following equipment and components in the figures below:

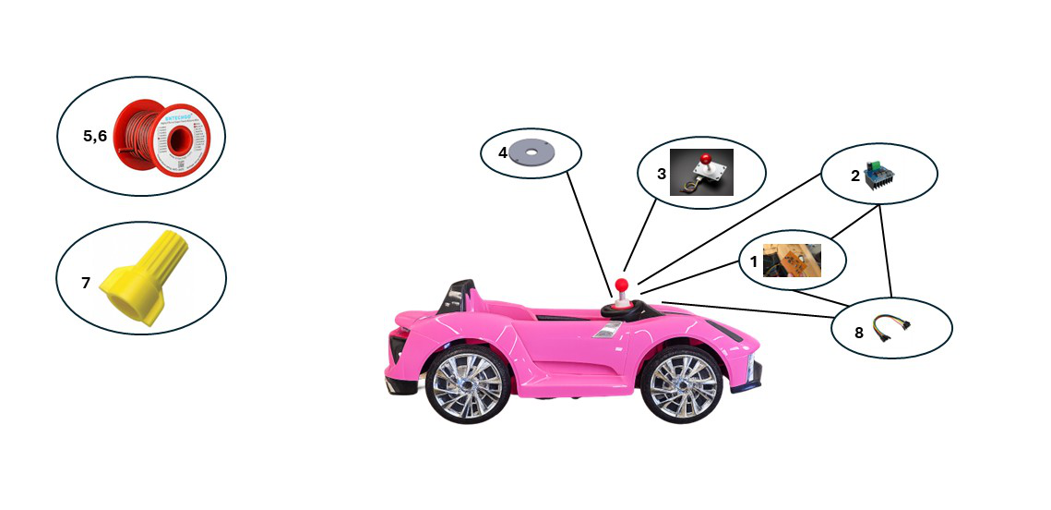
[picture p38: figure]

No. | Name of Part(s) | Qty.
1 | Circuit Board | 1
2 | IBT-2 H-Bridge Motor Controller | 3
3 | Joystick | 1
4 | Joystick Mount | 1
5 | 20 AWG Red Wire | 1
6 | 20 AWG Black Wire | 1
7 | Yellow Wire Nuts | 18
8 | Female to Female Jumper Wires | 24
9 | User Manual | 1

4. Materials & Tools Required
  4.1. List of Tools Needed
- Wire cutters/strippers.
- Phillips head screwdrivers (PH1.5 - PH4)

Please note: Not all materials and tools required for the assembly of this adaptation are provided in this kit. Fundamental wiring and assembly skills are required for the assembly of this project which will consist of stripping/cutting wire and screwing/unscrewing nuts and bolts. Please allow an adult who is familiar with said skills to carefully complete the assembly.

5. Procedures for Assembly & Operation

⚠ ALWAYS ENSURE THE BATTERY IS DISCONECTED BEFORE WORKING WITH ANY ELECTRICAL COMPONENTS ⚠

  5.1. Assembly️
1. Test all H-Bridge, joystick, and other electrical components before assembly
2. Remove the steering wheel. Look for a bolt at the base of the steering wheel and remove it. Unplug the wire and remove the steering wheel by pulling it up. Set aside.
3. Remove the dash by removing the screws in the four corners using a Philips head screwdriver. Unplug the wires attached to the right of the dashboard. Set aside.
4. Remove the cotter pin and washer at the front of the car, under where the dashboard used to be. Remove the screws that are adjacent to the washer.
5. Flip the car over
6. Remove the front axle assembly (seen in Figure 1).
  - Take out the four frame screws holding it to the frame.
  - Remove the cotter pin and washer at the base of the steering rod.
  - Lift the assembly up, set aside

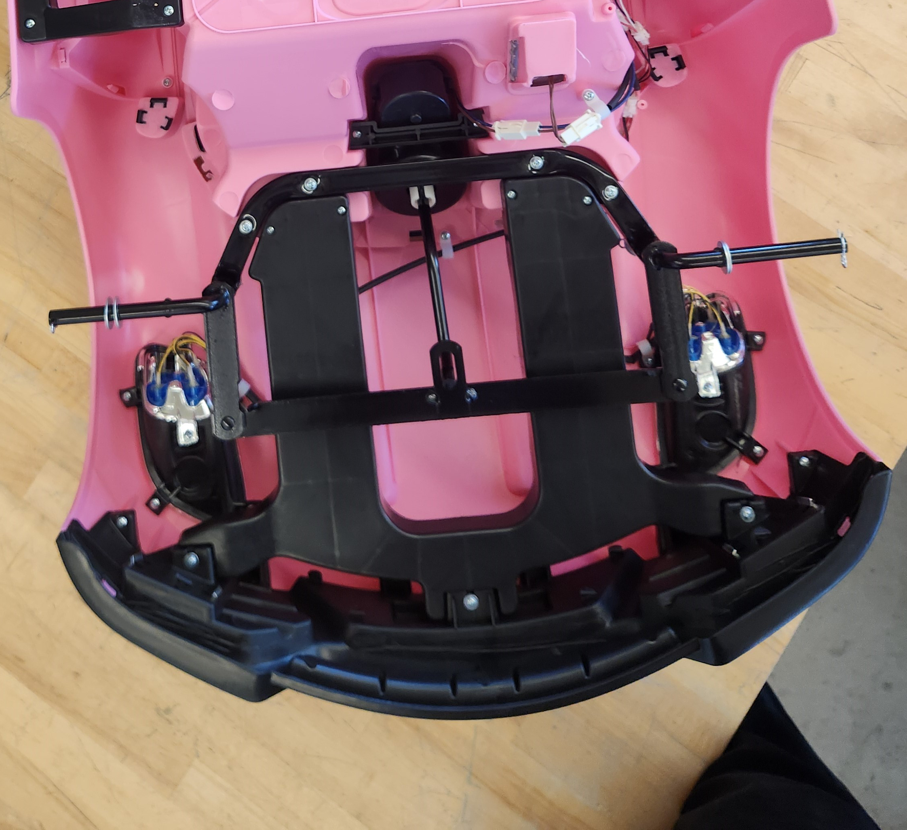
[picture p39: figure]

Frame Screws

Steering Motor Bracket

Figure 1: Bottom of Front end of car

7. Remove the steering motor bracket attached by a screw on either side (seen in Figure 1 above). Unplug the blue/brown wire attached to the steering motor. Pull the steering motor out and set aside.
8. Flip the car right-side-up.
9. Cut the Wires at the rear drive motors leaving 4 inches of wire attached to each motor. Do the same with the steering motor.
  - To find the rear drive motors (seen in Figure 2), move to the rear and look for a black and red wire set, under where the seat used to be.

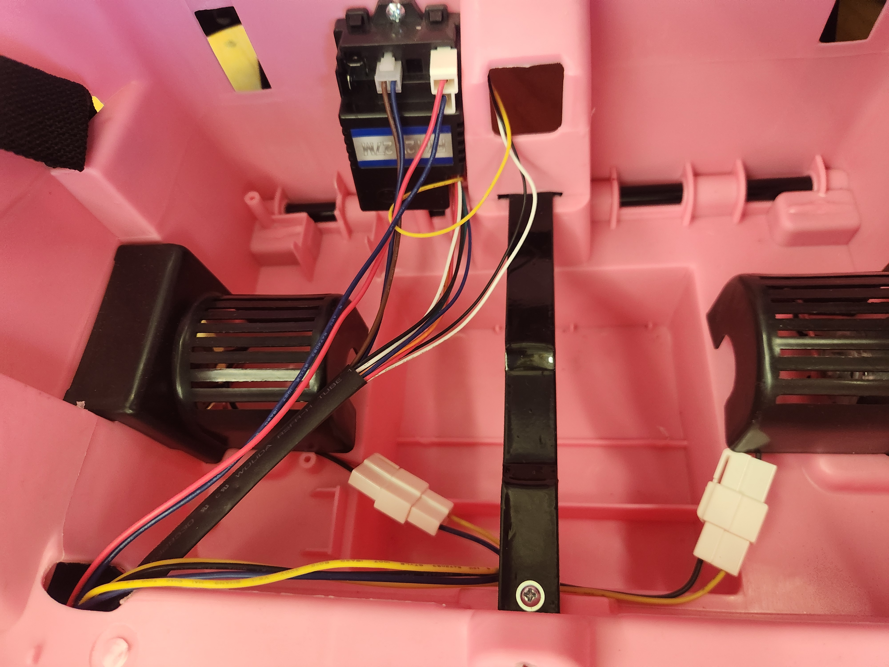
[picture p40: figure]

Driver Motor wires

Relay

Figure 2: Rear Compartement located under seat

10. Remove the relay mounted in the rear (seen in Figure 2 above) of the car attached by a single screw. Unplug all attached wires. Set aside.
11. Cut the wires on the battery wire assembly, ensure to keep some things attached:
  - The fuse that is located on the orange wire.
  - The charging port attached via a plug
  - Both connectors that attach to the battery
  - 4 inches of wire on either side, past the already stated components.
12. (optional) Remove all the remaining wires in the car OR leave them in incase of future retrofitting
13. Cut the steering rod to allow room for joystick. Using a bandsaw, cut off just above where the cotter pin is inserted from the car side of the rod.
14. Remove the back panel on the dashboard. Remove any wires ensuring to keep about 2 inches of wire on the start button.
15. Flip the car upside down and reattach the steering motor, ensuring:
  - The wires from the motor now go through the body, up to where the dashboard was placed.
  - All screws are properly tightened.
  - The cut steering rod is placed back into its former spot
  - The wheels are mounted properly.
16. Flip the car back up and attach the cotter pin and washer to the top of the steering rod
17. Screw in the steering motor mount.
18. Mount the joystick to the dashboard using the mount and mounting bolts.
  - Place the joystick on the inside of the dash, pointing out through the hole in the center. Place the mount on the other side of the dashboard and thread the bolts through the mount, dash, and joystick. The result should match that of Figure 3.

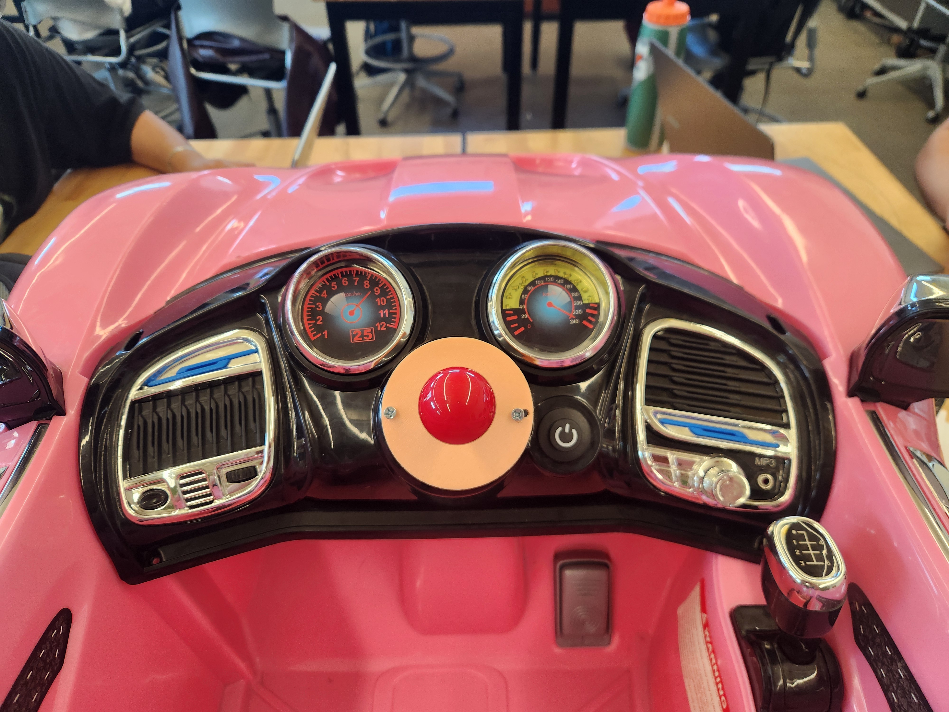
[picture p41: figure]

Figure 3: Mounted Joystick

19. Route the power wires from the battery to the front of the car. There are two power wires, a black and a red, and both split into four wires on the end. Ensure that the split end ends up in front of the car.
  - Start at the front, feeding the single wire end into the hole (Figure 4) located to the right of the dashboard

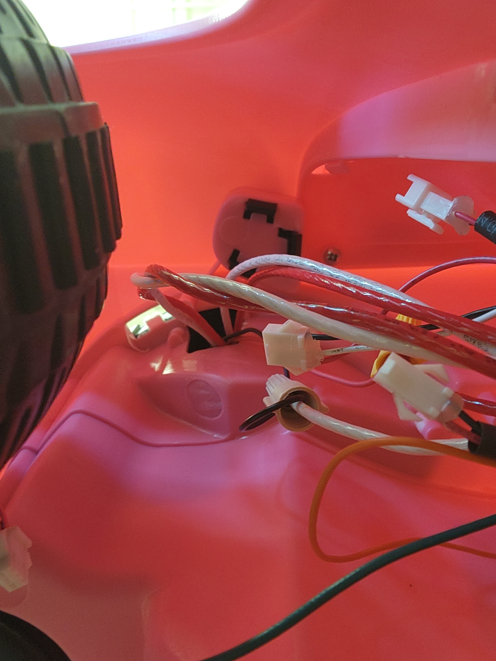
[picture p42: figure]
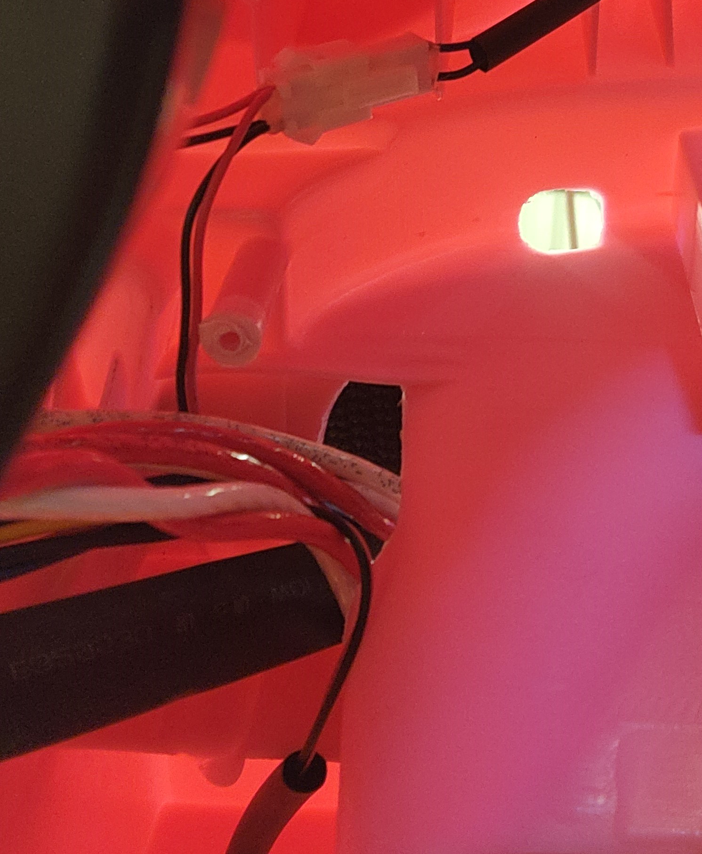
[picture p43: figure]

Figure 3

Figure 4

  - Route it above the black structural beams on the bottom of the car
  - Feed it through the hole in the rear that leads to the compartment under the seat (Figure 4).
20. Route wires from the rear drive motors to the front of the car as well, making use of the same holes used in step 19.
21. Place the motor drivers on the shelves located on either side of the steering column, one on the left and two on the right.
22. Begin attaching wires. Start by hooking up the steering motor driver, located to the left of the steering column. The brown wire should be attached to the M+ and the blue wire to the M-. Attach one of the logic wires, ensuring the black goes to the GND slot on the driver. Plug in the power wires, red to B+ and black to B-. Attach the other end of the logic wire to the PCB plug in labeled steering, ensuring the black goes to GND.
23. Do the same for each rear motor, plugging the logic wire into the PCB plug ins labeled left drive and right drive respectively. The result should look something like Figure 5.

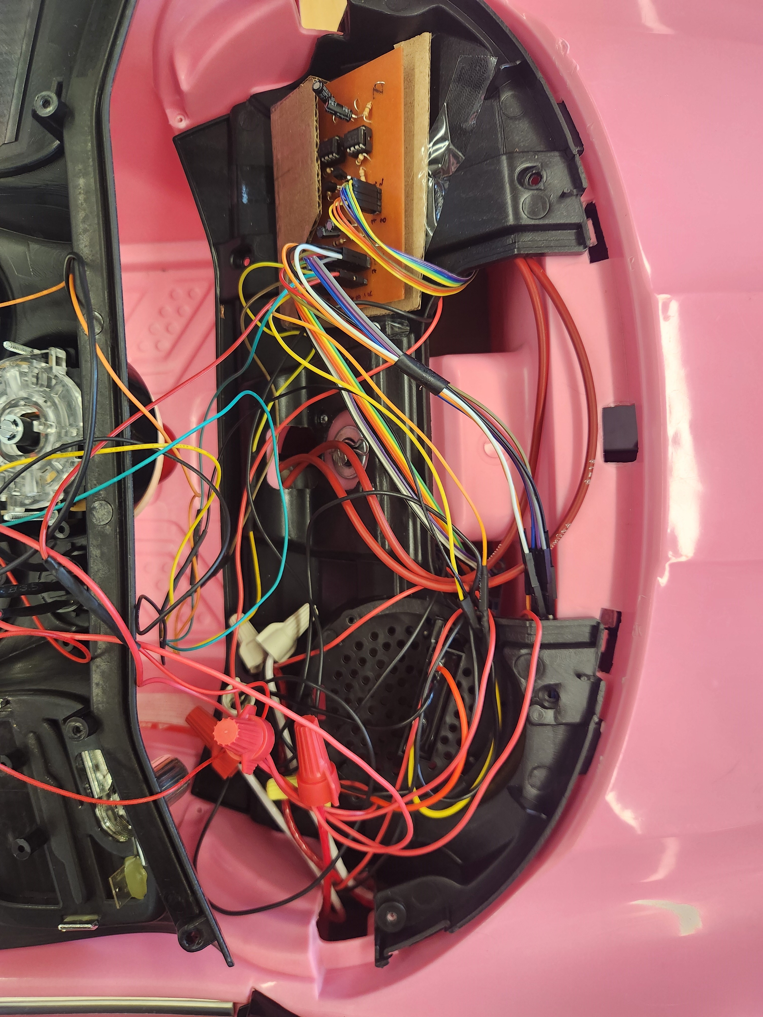
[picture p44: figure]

Figure 5: Wiring under dashboard

24. Now, attach the power converter to the last remaining power and ground wire with the supplied wire nuts. Attach the plug in the other end of the power converter to the PCB port labeled VCC
25. Attach the joystick wire into the PCB plug in labeled JYS, ensuring the red wire is on top (closest to the JYS label).
26. Re-mount the dashboard using the screws set aside earlier.
  5.2. Operation
- To operate, start by pressing the power button.
- To go forward, move the joystick up
- To go backward, move the joystick down
- To turn left, move the joystick left
- To turn right, move the joystick right
6. Maintenance Guideline
- Ensure the H-bridge correctly switches motor directions.
- Verify all directions: forward, backward, left, and right.
- Confirm that the motors stop when the joystick is released in any direction; this ensures the electrical system is operating as intended before use.
- Recharge the battery properly according to your specific battery manufacturer’s instructions.
- After any electrical maintenance, perform a test with an unloaded car (wheels are off the ground).
- Components should be visually inspected bi-monthly to check for natural wear or abnormal wear.
- Verify correct motor polarity by observing wheel rotation direction in response to forward and reverse inputs.
- Confirm that H-bridge outputs switch cleanly between states without simultaneous activation of opposing signals.
- Perform a post-maintenance electrical test by measuring supply voltage and checking for stable current draw during operation.
- Inspect all wiring connections for continuity, secure termination, and absence of loose or exposed conductors.
- Conduct a functional driving test after maintenance to ensure proper system response under load conditions.
7. Storage Guideline

⚠ PLEASE STORE THIS PRODUCT IN A COOL, DRY PLACE AND READ BELOW ⚠

- When the product is not in use, please have a knowledgeable adult disconnect the 12V power supply.
- Electrical components in this kit, such as the motor controllers, circuit board, and joystick, can develop corrosion if not stored in a cool dry place... resulting in damaged components and potential danger such as fire risks.
- It is also recommended that a knowledgeable adult tests battery voltage using a multimeter between every other charge session to ensure the battery is operating as intended.

Please note: The general temperature recommendation for storing a 12V battery can range from 41F°-68F°. As a general guideline, low temperatures can result in a decrease in battery performance, lifespan, and capacity. Allowing the battery to fully discharge may also result in damage. Please follow the guidelines provided by your specific battery manufacturer.

8. Troubleshooting Guideline
- Steering Problems:
  - Steering in wrong direction
    - Swap the M+ and M- wires attached to the steering motor driver.
  - Not steering enough
    - Ensure there are no wires blocking the wheels from steering far enough
    - Ensure the steering rod is attached properly
- Drive Problems:
  - Motors turning in opposite directions
    - Swap the M+ and M- wires attached to ONE of the rear motor drivers
  - Move backwards when forward pressed
    - Swap the M+ and M- wires attached to BOTH rear motor drivers
  - Left and right control forward and backward
    - Ensure the joystick wire is attached to the PCB with red on top.
9. Technical Support

⚠ IF AN EMERGENCY OCCURS DURING ASSEMBLY OR OPERATION CALL 911 IMMEDIATELY AND SAFELY DISCONNECT THE POWER SUPPLY IF POSSIBLE ⚠

For assistance with any minor issues, please refer to the Troubleshooting - Pg. 7 section of this manual.

For major problems, questions, or concerns please contact: cpkasayka@mavs.coloradomesa.edu

10. Spare Parts & Components
- Supplied spare parts include
  - 3 additional wire nuts
  - 3 feet of 20AWG wire
  - An extra female-female logic connector wire

CMU/CU Boulder Engineering Partnership Programs

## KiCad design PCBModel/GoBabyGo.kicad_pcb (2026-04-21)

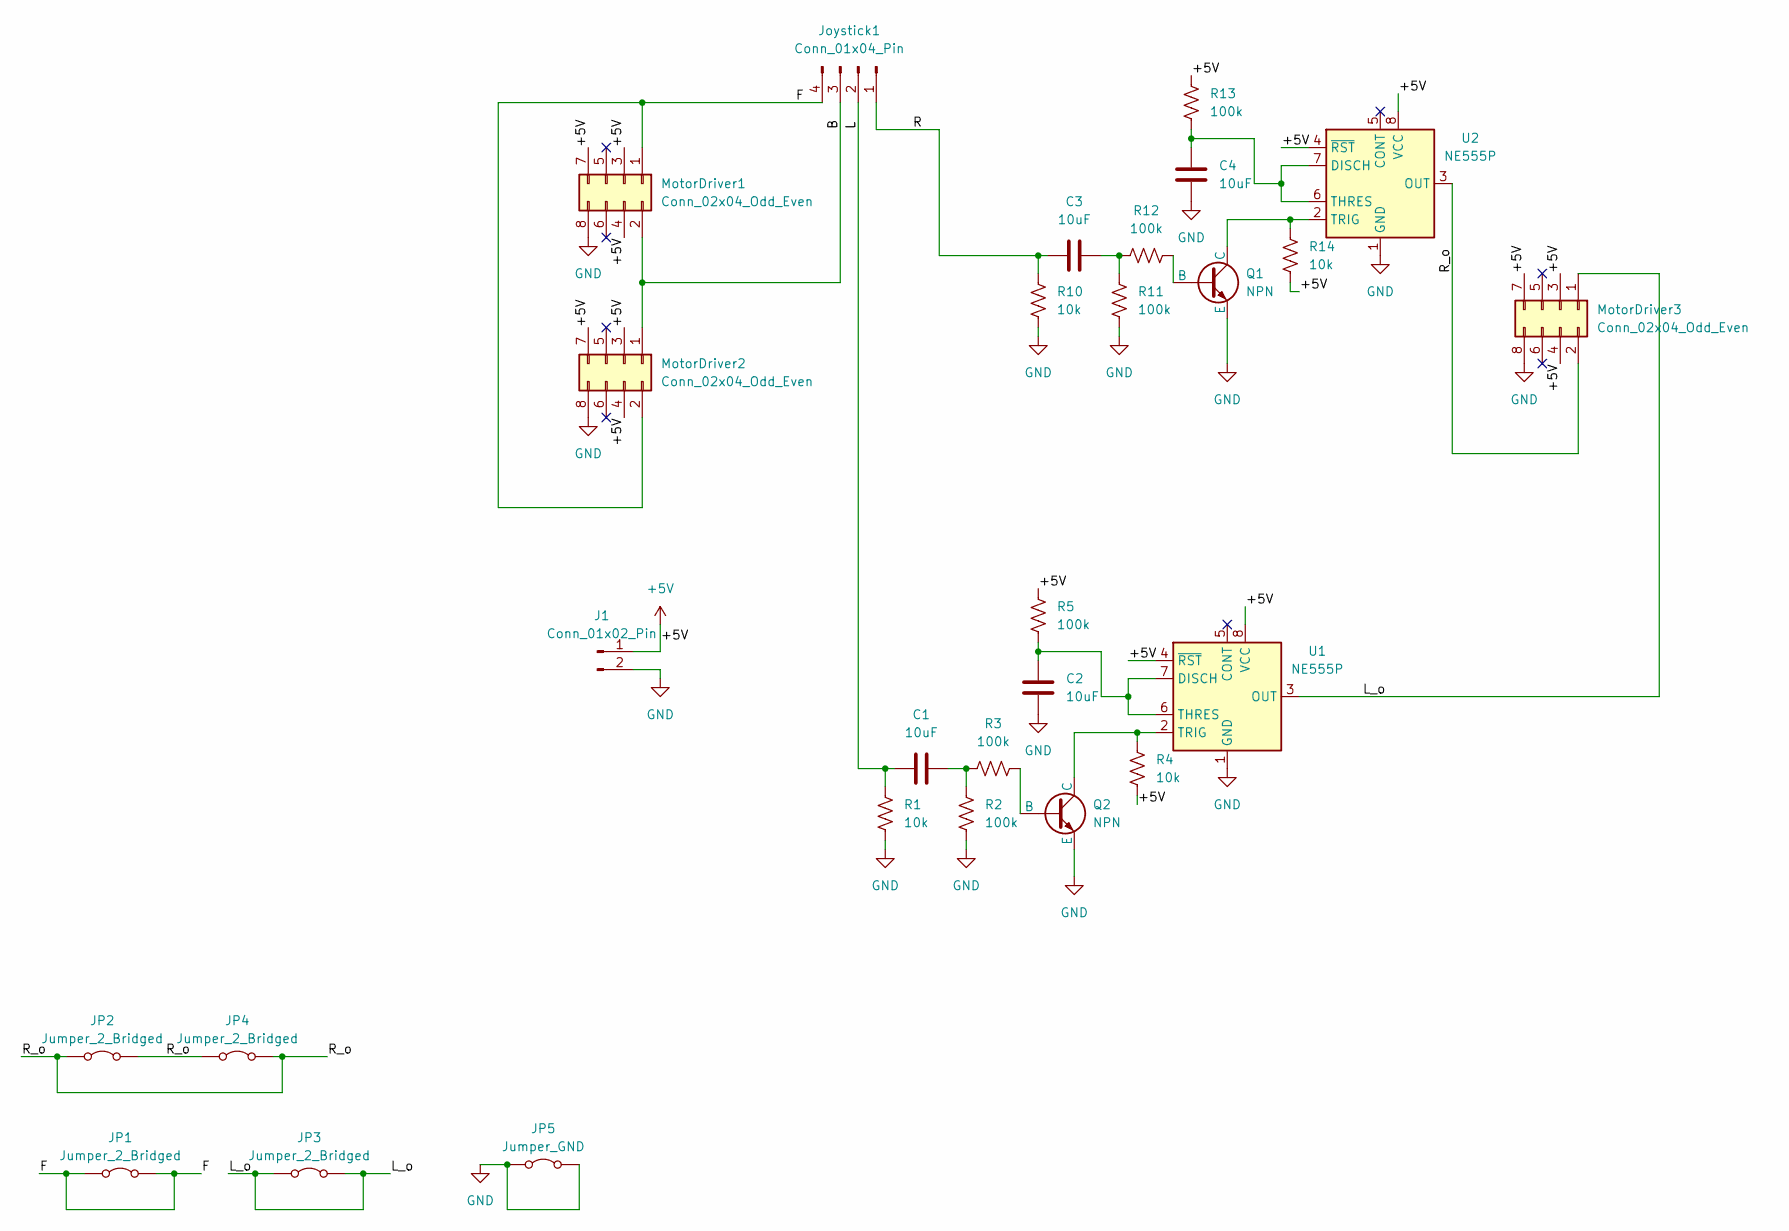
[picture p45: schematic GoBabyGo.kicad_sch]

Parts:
C1, C2, C3, C4: 10uF; C_Axial_L3.8mm_D2.6mm_P7.50mm_Horizontal
J1: Conn_01x02_Pin; PinHeader_1x02_P2.54mm_Horizontal
JP1, JP2, JP3, JP4: Jumper_2_Bridged; R_Axial_DIN0207_L6.3mm_D2.5mm_P5.08mm_Vertical
JP5: Jumper_GND; R_Axial_DIN0207_L6.3mm_D2.5mm_P5.08mm_Vertical
Joystick1: Conn_01x04_Pin; PinHeader_1x04_P2.54mm_Horizontal
MotorDriver1, MotorDriver2, MotorDriver3: Conn_02x04_Odd_Even; PinHeader_2x04_P2.54mm_Vertical
Q1, Q2: NPN; TO-92_Wide
R1, R4, R10, R14: 10k; R_Axial_DIN0207_L6.3mm_D2.5mm_P7.62mm_Horizontal
R2, R3, R5, R11, R12, R13: 100k; R_Axial_DIN0207_L6.3mm_D2.5mm_P7.62mm_Horizontal
U1, U2: NE555P; DIP-8_W7.62mm

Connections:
+5V: J1.1, MotorDriver1.3, MotorDriver1.4, MotorDriver1.7, MotorDriver2.3, MotorDriver2.4, MotorDriver2.7, MotorDriver3.3, MotorDriver3.4, MotorDriver3.7, R4.2, R5.1, R13.1, R14.2, U1.4 (~RST), U1.8 (VCC), U2.4 (~RST), U2.8 (VCC)
/B: Joystick1.3, MotorDriver1.2, MotorDriver2.1
/F: JP1.1 (A), JP1.2 (B), Joystick1.4, MotorDriver1.1, MotorDriver2.2
/L: C1.1, Joystick1.2, R1.1
/L_o: JP3.1 (A), JP3.2 (B), MotorDriver3.1, U1.3 (OUT)
/R: C3.1, Joystick1.1, R10.1
/R_o: JP2.1 (A), JP2.2 (B), JP4.1 (A), JP4.2 (B), MotorDriver3.2, U2.3 (OUT)
GND: C2.2, C4.2, J1.2, JP5.1 (A), JP5.2 (B), MotorDriver1.8, MotorDriver2.8, MotorDriver3.8, Q1.3 (E), Q2.3 (E), R1.2, R2.2, R10.2, R11.2, U1.1 (GND), U2.1 (GND)
unnamed: C1.2, R2.1, R3.1
unnamed: C3.2, R11.1, R12.1
unnamed: Q1.2 (B), R12.2
unnamed: Q1.1 (C), R14.1, U2.2 (TRIG)
unnamed: Q2.2 (B), R3.2
unnamed: Q2.1 (C), R4.1, U1.2 (TRIG)
unnamed: C2.1, R5.2, U1.6 (THRES), U1.7 (DISCH)
unnamed: C4.1, R13.2, U2.6 (THRES), U2.7 (DISCH)

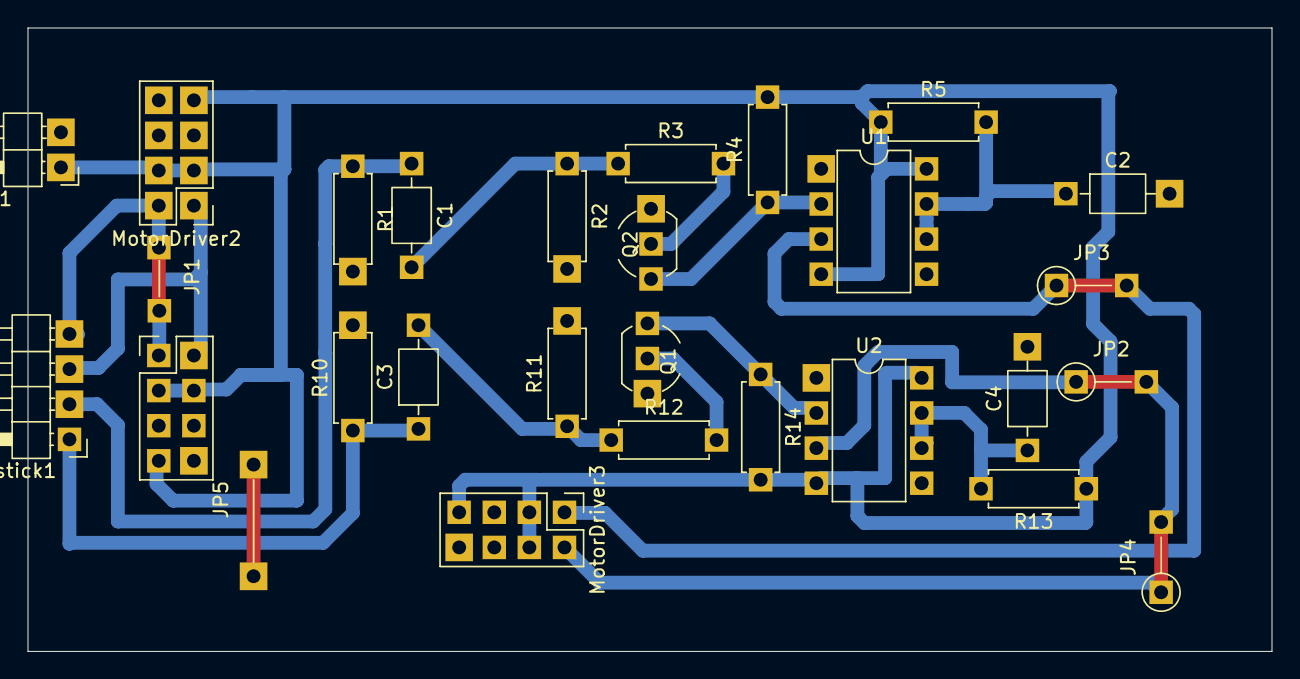
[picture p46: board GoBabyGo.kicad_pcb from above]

Board: 2 copper layers, 90.0 x 45.1 mm, 28 parts (0 on the bottom side), 16 nets.

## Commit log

2026-04-20 Added Images, datasheets, and PCB Model to the Github
    [GoBabyGo.kicad_pcb, GoBabyGo.kicad_sch]
2026-04-21 Minor PCB Model Fix
    [GoBabyGo.kicad_pcb]
2026-04-21 PCB review.
    [GoBabyGo.kicad_pcb, GoBabyGo.kicad_sch]
2026-04-28 Add section about the 555 timer and minor changes to the image
2026-04-28 schematic update
    [GoBabyGo.kicad_sch]
2026-05-01 Start of the README Report
    [GoBabyGo.kicad_sch]
2026-05-05 Added link for Mount and some more updates for the README
    [Joystick Mount 3.STL]
